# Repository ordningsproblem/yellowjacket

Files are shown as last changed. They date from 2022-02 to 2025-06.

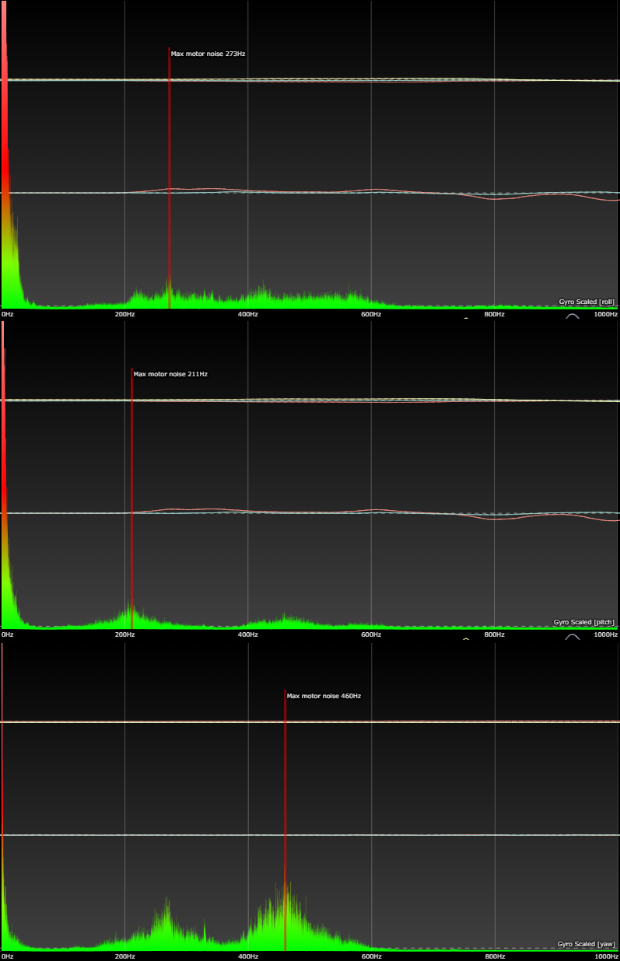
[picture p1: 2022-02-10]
Gyro data (clean build)/RPY gyro scaled.png

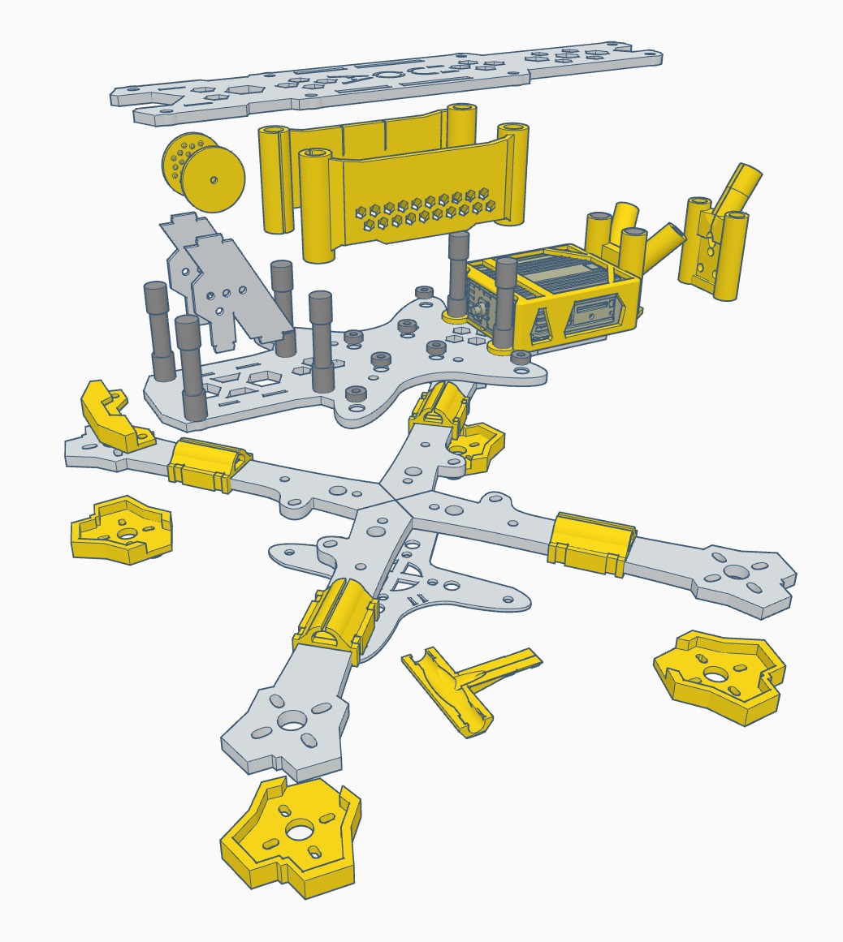
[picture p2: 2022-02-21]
Assembly instructions/assembly.jpg

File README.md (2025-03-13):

# yellowjacket

Freestyle FPV quadcopter frame

This is a carbon fibre freestyle frame designed with modularity in mind.
The main body is suitable for 5-inch to 7-inch propellers. Arms are available here in squished-X configuration (5 inch) as well as deadcat configuration (5 to 6 inch).
The frame in it's current design is cut from sheets/plates of carbon fibre composite, recommended thickness noted in DXF filenames and STEP-files. Additional mounts and parts are available as 3d-printable files.

The frame can be used with 30x30 (recommended for easy arm replacement) or 20x20 stacks. The frame is designed for a 20x20-25.5x25.5mm VTX (Caddx Vista, HDZero, Walksnail or analog) but can hold a full size DJI Air Unit using a TPU cage (noted in DXF file name).
The frame is designed to carry an action camera like the GoPro Hero with low displacement on center of gravity.

All TPU is designed for 6mm knurled standoffs and will be lose and cause gyro noise if used with smaller standoffs.

Arms of all styles will not always be updated at the same time as focus lies on X-configuration 5-inch. Feel free to contact me for arm options and updates.

If you don't want to cut the frame yourself I'm trying to keep the current version available with hardware at: https://armattanproductions.com/pages/shop_product_grid/7553

-------------------------
### V1.4.2 ###

-Added deadcat 6-inch arm kit



-------------------------
### V1.4.1 ###

-Added deadcat 5-inch arm kit and extended O3 camplates



-------------------------

### V1.4 ###

-Added split body design with new electronics mounting holes in one-file format in STEP, OBJ, and Fusion360 F3D formats

-DJI O3 compatible both with standard cam plates and added TPU front mount for less wide angle obstuction (Note: TPU front mount for O3 requires 200mm camera cable) 
(Should be Walksnail compatible, not verified as of 2023-06-15)

-Added complete Humblebee 3-inch freestyle+cinewhoop frame design

-Note: Most TPU parts for the old body can easily be modified for split deck as deck height is the main difference.  

YJ1.4:





Humblebee:




------------------



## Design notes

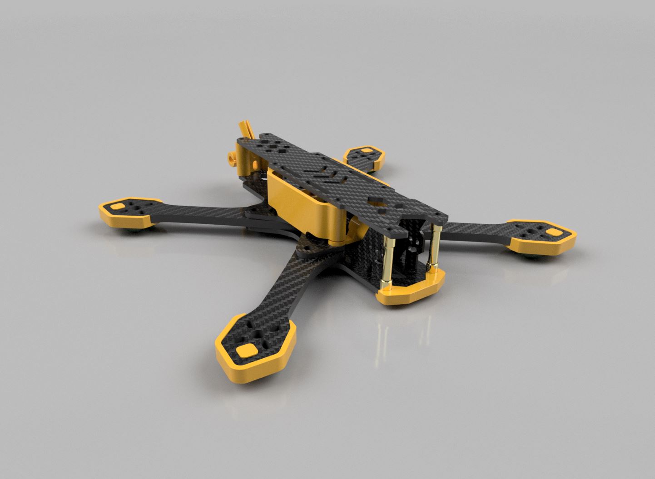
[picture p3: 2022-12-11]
Yellowjacket v1.4 (Splitbody)/Render-front.JPG

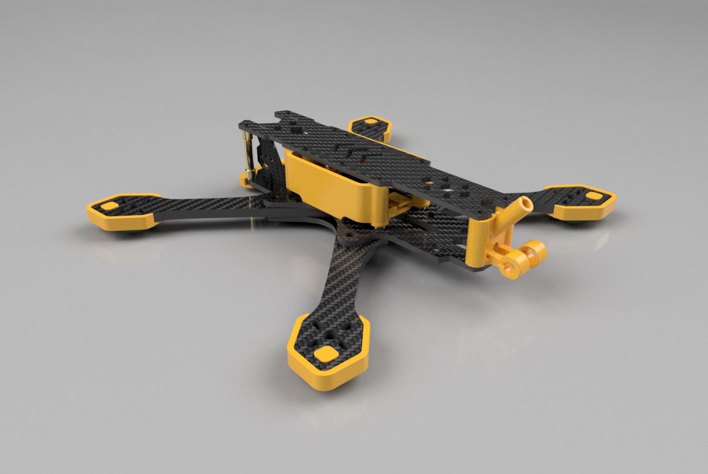
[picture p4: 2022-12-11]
Yellowjacket v1.4 (Splitbody)/Render-back.JPG

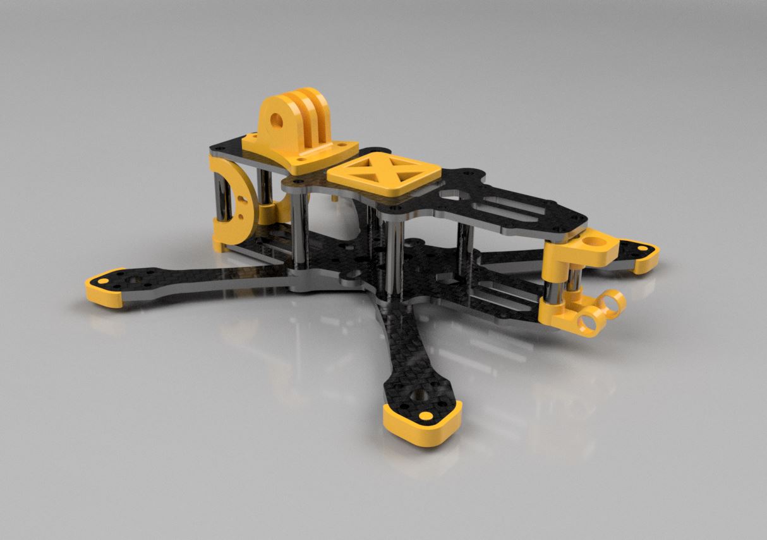
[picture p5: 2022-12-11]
Humblebee 3-inch frame/Render-back.JPG

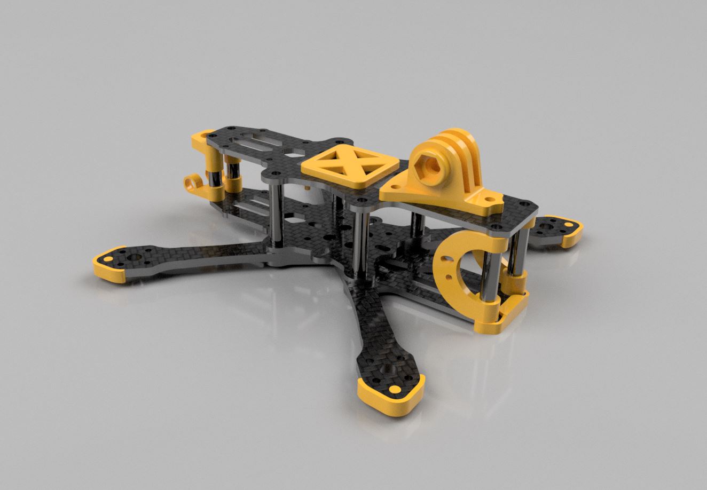
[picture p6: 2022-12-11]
Humblebee 3-inch frame/Render-front.JPG

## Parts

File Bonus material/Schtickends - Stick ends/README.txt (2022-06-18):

These stickends are made for common brass inserts from amazon. 
Print in resin, brush extra resin on insert contact surfaces, press in place, cure in UV light.

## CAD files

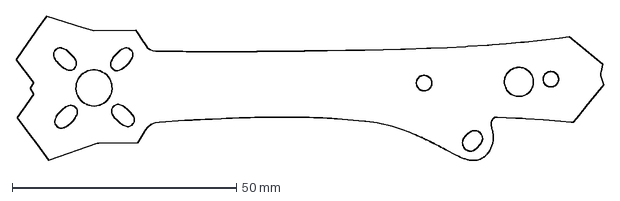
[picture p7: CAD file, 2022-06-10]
DXF/V1.2 - Main Tank - Durability upgrade/Main_Tank_-_X-arm-3-Hole-5mm-Durability.dxf
131.0 x 32.1 mm

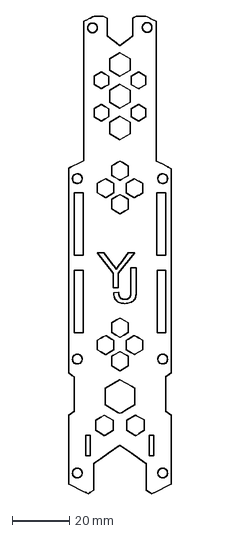
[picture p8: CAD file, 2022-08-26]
DXF/V1.3 - Main Tank - Tolerance update/1x-Main_tank_-_Top_plate-NewStrapPlacement-AirUnit-Vista-2.5mm.dxf
36.0 x 167.5 mm

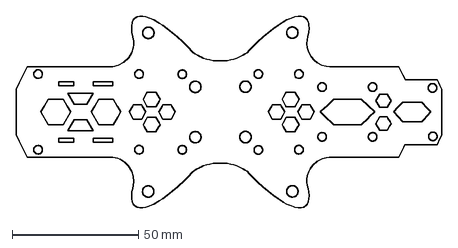
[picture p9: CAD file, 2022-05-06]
DXF/V1.1 frame - main plate (long air unit) updated with rounded tabs 3mm.dxf
168.5 x 75.7 mm

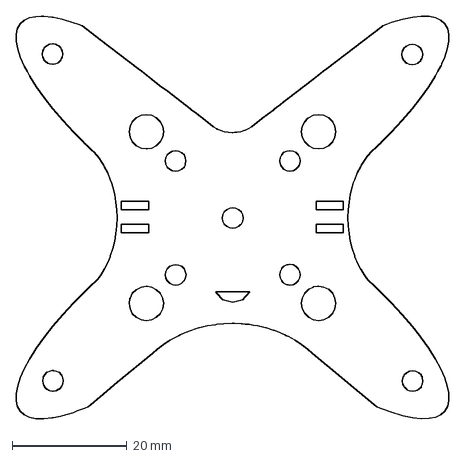
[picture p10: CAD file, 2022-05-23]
DXF/V1.2 - Main Tank - Durability upgrade/Main_Tank_-_Bottom_plate_Center-hole-3mm.dxf
75.5 x 70.2 mm

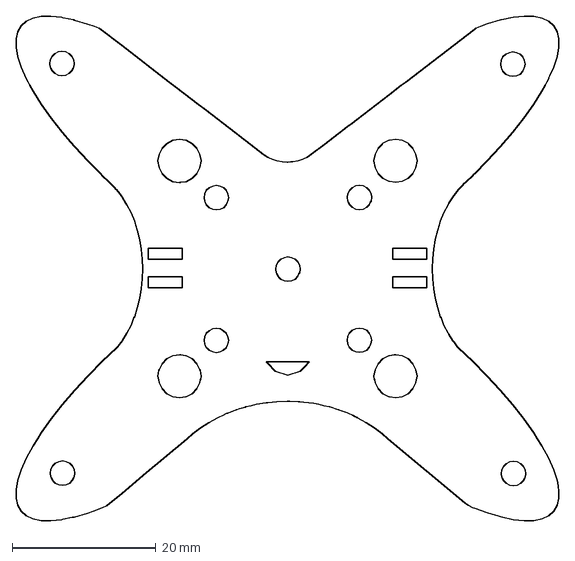
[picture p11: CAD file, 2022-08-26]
DXF/V1.3 - Main Tank - Tolerance update/1x-Main_Tank_-_Bottom_plate_Center-hole-3mm.dxf
75.5 x 70.2 mm

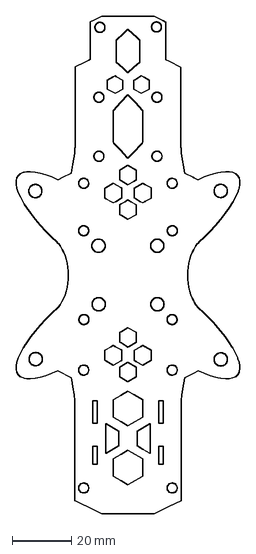
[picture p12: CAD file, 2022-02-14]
DXF/V1.1 frame - main plate (long air unit) 3mm.dxf
75.7 x 168.5 mm

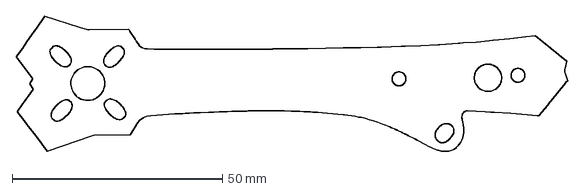
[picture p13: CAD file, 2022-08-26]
DXF/V1.3 - Main Tank - Tolerance update/4x-Main_Tank_-_X-arm-3-Hole-5mm.dxf
131.0 x 32.1 mm

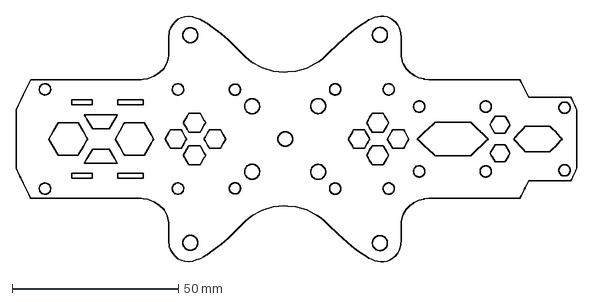
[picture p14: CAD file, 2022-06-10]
DXF/V1.3 - Main Tank - Tolerance update/1x-Main_tank_-_Main_plate_Center-hole-AirUnit-Vista-3mm.dxf
168.5 x 73.8 mm

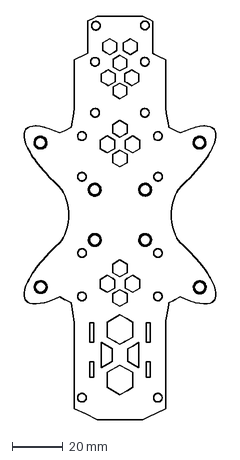
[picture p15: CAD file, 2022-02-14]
DXF/V1 frame -main plate (short) 3mm.dxf
75.7 x 159.2 mm

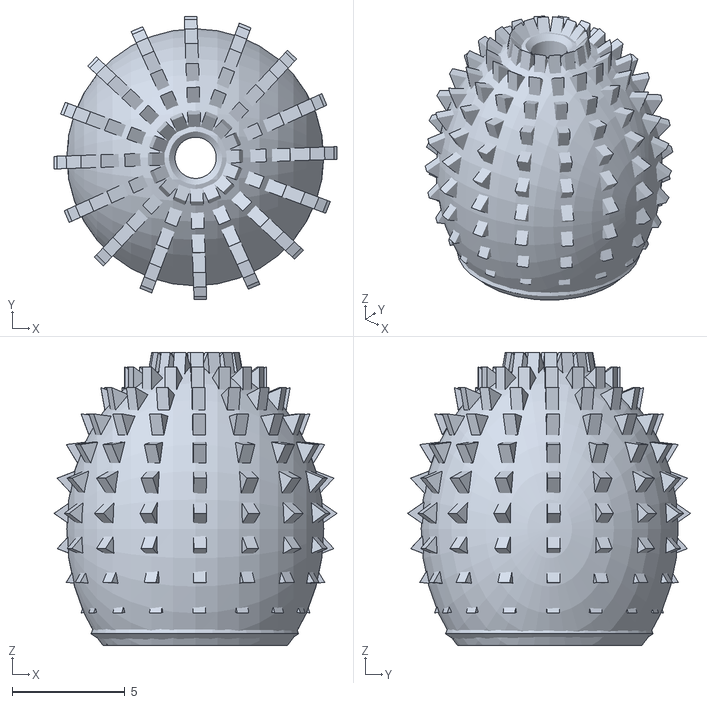
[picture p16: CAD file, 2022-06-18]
Bonus material/Schtickends - Stick ends/Schtickend ~4.68mm-insert.stl
12.5 x 12.5 x 13.0

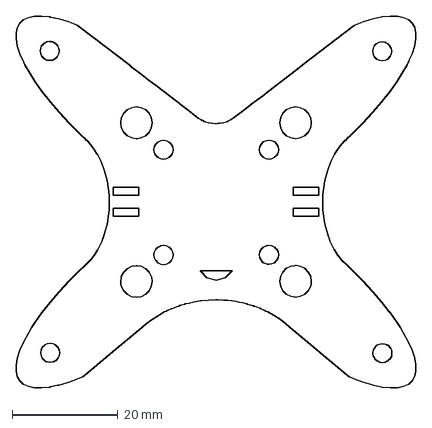
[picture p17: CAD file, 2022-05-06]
DXF/V1.1 bottom plate 2-3mm.dxf
75.5 x 70.2 mm

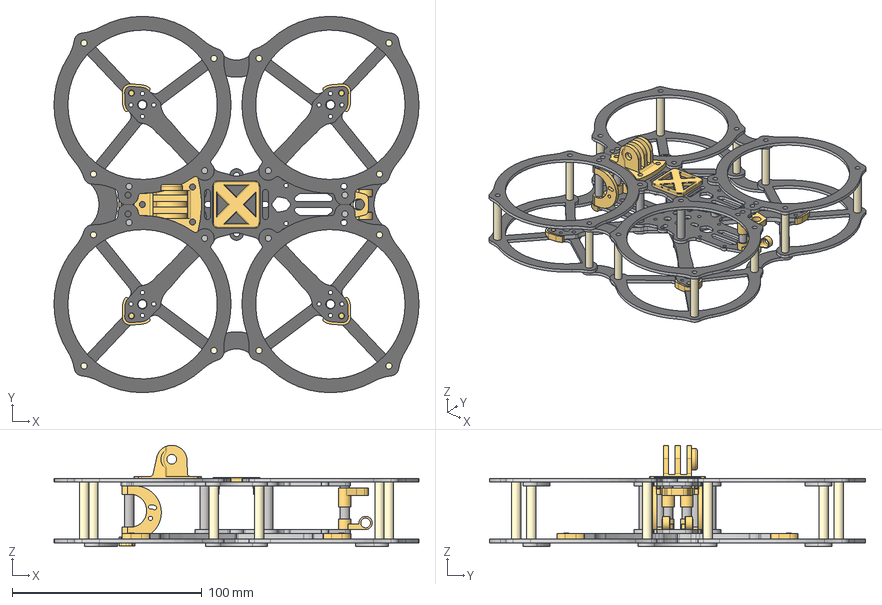
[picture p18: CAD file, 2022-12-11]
Humblebee 3-inch frame/Humblebee-3.step
192.2 x 198.1 x 53.4 mm

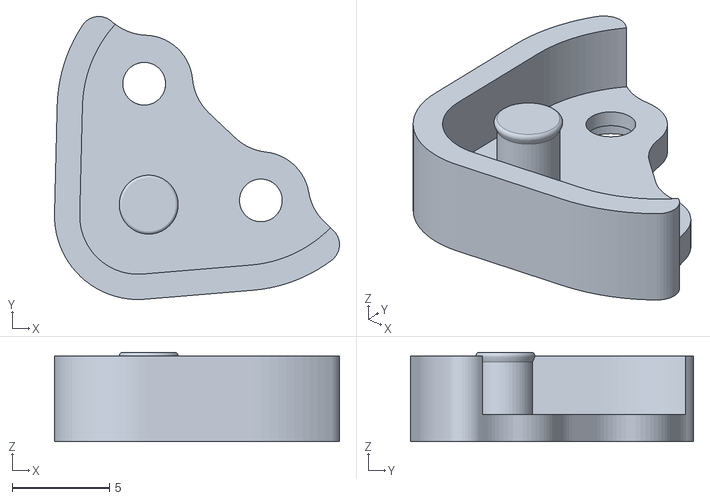
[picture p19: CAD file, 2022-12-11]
Humblebee 3-inch frame/TPU STL/foot.stl
14.7 x 14.6 x 4.60

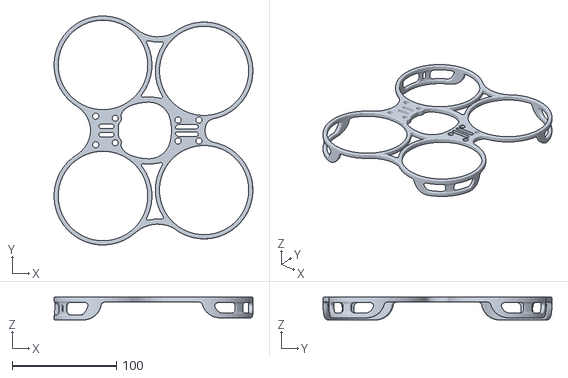
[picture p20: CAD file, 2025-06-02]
Humblebee V2 DC3/Hard plastic STL/guards.stl
190.4 x 219.3 x 22.0

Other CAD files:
Humblebee V2 DC3/TPU STL/FCadapt20to25-5.stl
TPU STL/5mm standoff STLs/Multi SMA 5mm.stl
TPU STL/hero8-30deg.stl
Yellowjacket v1.4 (Splitbody)/Deadcat kit & O3 cam plates/Front DC6.step
Bonus material/Schtickends - Stick ends/Schtickend 5mm-insert.stl
DXF/V1 frame - top plate (short) 3mm.dxf
DXF/V1-V1.1 - 5 inch dc front arm.dxf
DXF/V1-V1.1 - 5 inch dc rear arm.dxf
DXF/V1-V1.1 - 5 inch x 3-hole.dxf
DXF/V1-V1.1 - 7 inch brace.dxf
DXF/V1-V1.1 - 7 inch dc front arm.dxf
DXF/V1-V1.1 - 7 inch dc rear arm.dxf
DXF/V1.1 frame - top plate (long air unit) 3mm.dxf
DXF/V1.3 - Main Tank - Tolerance update/2x-All versions_-_Cam_mount-1.5mm.dxf
DXF/cam mount.dxf
Humblebee 3-inch frame/TPU STL/RX-antennamount-left.stl
Humblebee 3-inch frame/TPU STL/RX-antennamount-right.stl
Humblebee 3-inch frame/TPU STL/bumper.stl
Humblebee 3-inch frame/TPU STL/cam-mount-left.stl
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

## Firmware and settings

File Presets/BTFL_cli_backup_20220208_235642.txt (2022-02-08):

set gyro_lpf1_static_hz = 0
set gyro_lpf2_static_hz = 0
set dyn_notch_count = 0
set dyn_notch_q = 500
set gyro_lpf1_dyn_min_hz = 275
set gyro_lpf1_dyn_max_hz = 550
set dshot_bidir = ON
set simplified_gyro_filter_multiplier = 110
set rpm_filter_fade_range_hz = 100

set dterm_lpf1_dyn_min_hz = 80
set dterm_lpf1_dyn_max_hz = 110
set dterm_lpf1_dyn_expo = 8
set dterm_lpf1_type = BIQUAD
set dterm_lpf1_static_hz = 0
set dterm_lpf2_static_hz = 0
set p_pitch = 58
set i_pitch = 120
set d_pitch = 59
set f_pitch = 131
set p_roll = 56
set i_roll = 115
set d_roll = 52
set f_roll = 125
set p_yaw = 56
set i_yaw = 115
set f_yaw = 125
set d_min_roll = 39
set d_min_pitch = 44
set feedforward_smooth_factor = 35
set feedforward_jitter_factor = 9
set simplified_i_gain = 115
set simplified_d_gain = 130
set simplified_pi_gain = 125
set simplified_feedforward_gain = 105
set simplified_dterm_filter = OFF

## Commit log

2022-02-08 Update 5 inch dc rear arm.svg
2022-02-10 gyro info
2022-02-10 Update RPY gyro scaled freq throttle resp.png
2022-02-14 DXF fix
    [5 inch dc front arm.dxf, 5 inch dc rear arm.dxf, 5 inch x 3-hole.dxf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]
2022-02-14 Measurement fix
    [5 inch dc front arm.dxf, 5 inch dc rear arm.dxf, 5 inch x 3-hole.dxf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]
2022-02-14 Update main plate (long air unit).dxf
    [main plate (long air unit).dxf]
2022-03-22 BEEP BEP
    [Air Unit SMA.stl, Single SMA pigtail.stl, air unit mount.stl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]
2022-03-28 Create Single SMA pigtail 5mm.stl
    [Single SMA pigtail 5mm.stl]
2022-03-28 Update Single SMA pigtail 5mm.stl
    [Single SMA pigtail 5mm.stl]
2022-03-28 Create Single SMA pigtail 5mm SOLID.stl
    [Single SMA pigtail 5mm SOLID.stl]
2022-05-06 Alternative parts (increased durability)
    [bottom plate 2mm NEW.dxf, main plate (long air unit) NEW ROUNDED 3mm.dxf]
2022-05-23 V1.2 Main Tank update
    Updated parts for durability, noted recommended thickness
    [All versions - Cam mount 1-1.5mm.dxf, All versions - OLD cam mount.dxf, Main_Tank_-_Bottom_plate_3mm-CARBON_FIBER-3mm-Black.dxf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]
2022-05-23 Update file names
    [Main_Tank_-_Bottom_plate_Center-hole-3mm.dxf, Main_Tank_-_X-arm-3-Hole-5mm-Durability.dxf, Main_tank_-_Main_plate_Center-hole-3mm-AirUnit-Vista.dxf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]
2022-05-23 Add underbody rear antenna mount
    [Rear under-body RX antenna mount.stl]
2022-06-01 Feet for thicker arms
    [foot 4mm.stl, foot 5mm.stl]
2022-06-07 Update foot 5mm.stl
    [foot 5mm.stl]
2022-06-07 update bottom plate thickness
    [front bumper 2-2.5mm.stl, front bumper 3mm.stl]
2022-06-07 cam shim
    [cam shim.stl, cam shims.stl]
2022-06-07 Update cam shim.stl
    [cam shim.stl]
2022-06-10 Stress fracture fix
    [Main_Tank_-_X-arm-3-Hole-5mm-Durability.dxf, Main_tank_-_Main_plate_Center-hole-3mm-AirUnit-Vista.dxf]
2022-08-26 Tolerance update
    [All versions - Cam mount 1-1.5mm.dxf, Main_Tank_-_Bottom_plate_Center-hole-3mm.dxf, Main_Tank_-_X-arm-3-Hole-5mm-Durability.dxf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]
2022-08-26 Production update
    [1x-Main_Tank_-_Bottom_plate_Center-hole-3mm.dxf, 1x-Main_tank_-_Main_plate_Center-hole-AirUnit-Vista-3mm.dxf, 1x-Main_tank_-_Top_plate-NewStrapPlacement-AirUni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]
2022-12-11 1.4 Split Body
    [1x-Main_Tank_-_Bottom_plate_Center-hole-3mm.dxf, 1x-Main_tank_-_Main_plate_Center-hole-AirUnit-Vista-3mm.dxf, 1x-Main_tank_-_Top_plate-NewStrapPlacement-AirUni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]
2023-01-16 passthrough hole relocation
    [Yellowjacket 1.4.step]
2023-03-30 Correction holes + new TPU
    [Singe antenna (vista) ELRS.stl, Yellowjacket 1.4.step, single antenna (vista) Crossfire.stl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]
2023-05-25 assembly instructions
2023-05-31 dogbone milling fix
    [O3 cam front cage alternative.stl, VTX TPU screw holder.stl, Yellowjacket 1.4.step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]
2023-06-21 New TPU
    [Air Unit 5.5mm standoffs (for v1.4).stl, Gopro stock mount.stl, HGLRC M100 top mount.stl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]
2023-06-21 Create Rear underside CRSF antenna mount.stl
    [Rear underside CRSF antenna mount.stl]
2023-06-30 Create O3 cam front cage alternative (filter compatible).stl
    [O3 cam front cage alternative (filter compatible).stl]
2023-07-05 Update O3 cam front cage alternative (filter compatible).stl
    [O3 cam front cage alternative (filter compatible).stl]
2023-07-07 Create quad mustache.stl
    [quad mustache.stl]
2023-09-05 Deadcat 5 Kit (and O3 extended cam plates)
    [Front DC.step, O3 camplate L.step, Rear DC.step]
2023-09-06 O3 update
    [O3 camplate L.step, O3 camplate TPU.stl]
2024-02-26 TPU update
    [Antennamount o2 Airunit (new cage).stl, Gopro stock mount.stl, o2 Airunit new cage (no RX antenna).stl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]
2025-03-13 O4 kit
    Hey it's me again..
    [Antennamount o2 Airunit (new cage).stl, O4 TPU insert L.stl, O4 TPU insert R.stl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]
2025-06-02 Humblebee V2 DC3
    New frame
    [35380-frontbottom3-CARBON_FIBER-2mm-Black.dxf, 35381-rearbottom3-CARBON_FIBER-2mm-Black.dxf, 35382-top3-CARBON_FIBER-2mm-Black.dxf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]
2025-06-02 Humblebee V2 DC3
    [35380-frontbottom3-CARBON_FIBER-2mm-Black.dxf, 35381-rearbottom3-CARBON_FIBER-2mm-Black.dxf, 35382-top3-CARBON_FIBER-2mm-Black.dxf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]
2025-06-06 Update on arm holes (DXF)
    Support for both 9x9 and 12x12
    [35383-dcfront3-CARBON_FIBER-3mm-Black.dxf, 35384-dcrear3-CARBON_FIBER-3mm-Black.dxf]
2026-04-30 FC adapter
    [FCadapt20to25-5.stl]
